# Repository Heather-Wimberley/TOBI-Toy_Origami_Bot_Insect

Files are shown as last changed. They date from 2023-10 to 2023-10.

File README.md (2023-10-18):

# Toy Origami Bot Insect (TOBI)

This repo details all of the supplementary files for a final-year engineering project.

## Description

Origami is an art form that folds paper into various shapes. These can range from a simple
butterfly to very many complicated patterns such as an intricate dragon. This idea has inspired
an engineering manufacturing technique, where the frame of a robot or other mechanical parts
are made to be assembled from a two-dimensional sheet to a three-dimensional pattern. This
allows for a more cost-effective manufacturing process and allows for easier storage and assembly
of the design. Translating the idea of folding paper to more robust objects can prove difficult
due to the complicated nature of the designs and the specialist equipment often required to
build these origami materials so this process is what the project aims to solve. This will be
done by designing a frame for a legged robot that will be used to entertain a cat. The robot
will need to be able to autonomously navigate a house while avoiding any obstacles in it.

A picture of the final robot made from the closed hardboard frame is found below.

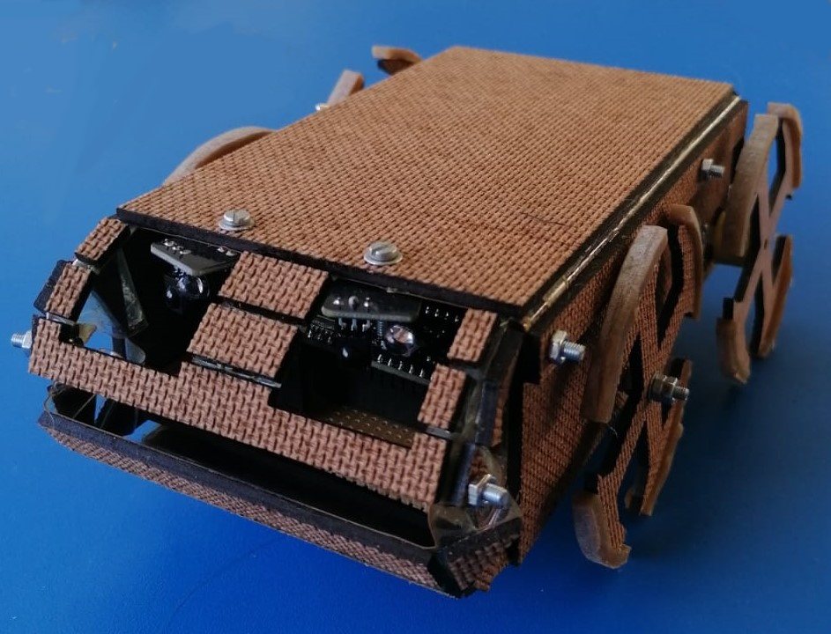
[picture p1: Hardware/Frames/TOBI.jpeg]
TOBI


## Contents
### Software

This file contains all the code written for the robot including design algorithms. The following files can be found:

- [OrigamiRobotAvoidance](Software/OrigamiRobotAvoidance.cpp):  The main function created for the robot to allow to avoid objects.
- [CurvedFrameSolver](Software/CurvedFrameSolver.mlx):  The algorithm is designed to be used with the curved frame to get the dimensions to be used for the curve. The height of the body and of the system and the number of segments can be changed to get the correct measurements. These are all assumed to be in mm.
- [Pickup](Software/Pickup.cpp):  This function contains the code for pickup detection working in isolation with the MXC6655. Due to time constraints, it was not integrated with the object avoidance.

### Hardware

This file contains the budget to see all components as well as all the .stl files of the whegs and each frame. This can be exported to pdfs to cut them using a laser cutter. A detailed breakdown of the files is:

- [Budget](Hardware/Budget.xlsx): This file is a spreadsheet of all the components, their prices and where they were acquired from. It also has the power budget done to determine battery requirements.
- [Electronics](Hardware/Electronics):  This folder contains the images needed to build the electronics of the robot. It includes a circuit diagram of the system as well as the veroboard design. The veroboard design includes the pin numbers that were used for the microcontroller.
- [Frames](Hardware/Frames):  This folder contains the stl files of all the frames designed. Although these are 3D, they are meant to be exported to a 2D pattern (top view) to be cut and the depth to the material has been added to show the different material parts. There are 5 designs of which two are made of posterboard and PET (labelled card) and three hardboard and vinyl (labelled wood). These materials each have different frame styles and assembly methods have been recorded in the associated paper.
- [Whegs](Hardware/Whegs):  This folder contains the stl files for the wheg design including the wheel caps for the back whegs and the two different versions that were designed.

## Authors

[Heather Wimberley](https://github.com/Heather-Wimberley)

## License

Open Source Project as long as creators are linked.

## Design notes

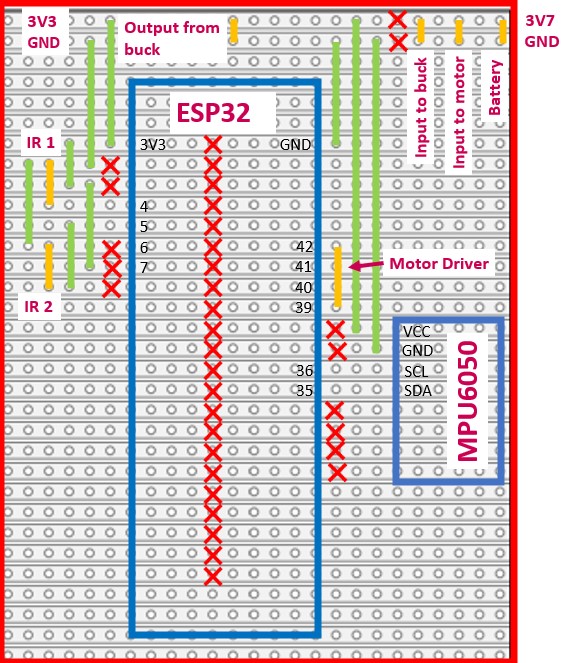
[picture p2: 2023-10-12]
Hardware/Electronics/Veroboard.jpg

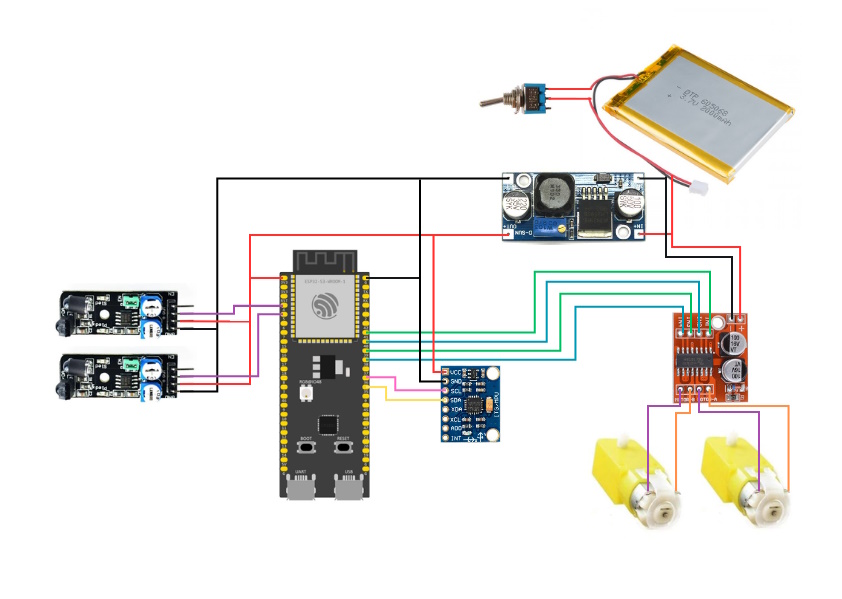
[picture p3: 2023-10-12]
Hardware/Electronics/Circuit Diagram.jpg

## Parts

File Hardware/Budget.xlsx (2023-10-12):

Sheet: Final Budget
Project Budget
Component | Price per unit | Quantity | Bought (B)/Owned (O) | Price | Total
HKD IR SENSOR SWITCH MODULE | 35.01 | 4 | B | 140.04 | 1049.64
BMT 3 AXIS ACCELEROMETER MPU6050 | 49 | 1 | B | 49
MX1616 H-BRG DC MOTOR DRIVER | 30 | 1 | B | 30
GEARED MOTOR 48:1 3-6VDC | 27 | 2 | B | 54
ESP32-S3-DevkitC-1 | 260 | 1 | O | 260
Battery LiPo 2000mAh 3.7V | 112 | 2 | B | 224
DC-DC STEP-DOWN | 52 | 1 | B | 52
Laminating sheets A4 | 1.4 | 9 |  | 12.6
Hardboard A3 | 18 | 4 |  | 72
Gluestick | 28 | 1 |  | 28
Posterboard (500gsm) | 16 | 8 |  | 128

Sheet: Electronics Comparison
Microcontrollers | Price | Link | Sensors | Price | Link | Battery | Price | Link
Raspberry Pi Zero W | 320 |  | BMT IR OBSTACLE AVOIDANCE SENSOR | 15 | https://www.communica.co.za/products/bmt-ir-obstacle-avoidance-sensor?variant=31803174682697 | HKD DC/DC BOOST MOD+USB 2-24V 2A | 29 | https://www.communica.co.za/products/hkd-dc-dc-boost-mod-usb-2-24v-2a?variant=45065768534316
ESP32-S3-DevkitC-1 | 260 | https://www.digikey.co.za/en/products/detail/espressif-systems/esp32-s3-devkitc-1-n32r8v/15970965 | HKD IR SENSOR SWITCH MODULE | 35.01 | https://www.communica.co.za/products/hkd-ir-sensor-switch-module?variant=31933933682761 |  | 26 | https://www.robofactory.co.za/power-converters/489-mt3608-dc-dc-2a-boost-module-2v-24v-with-micro-usb.html
 |  |  | BMT 3 AXIS ACCELEROMETER MPU6050 | 49 | https://www.communica.co.za/products/bmt-3-axis-accelerometer-mpu6050?variant=31667845464137 | 2XAA BATTERY HOLDER WITH SWITCH | 12 | https://www.communica.co.za/products/2xaa-battery-holder-with-switch?variant=17184817086537
 |  |  |  |  |  | AA Alkaline batteries x4 | 50 | https://www.takealot.com/energizer-e91bp3-1-1-5v-max-alkaline-aa-card-3-1-free/PLID69307304
 |  |  | MX1616 H-BRG DC MOTOR DRIVER | 30 | https://www.communica.co.za/products/bdd-mx1616-h-brg-dc-motor-driver?variant=45185422983468 | AA Lithium batteries x2 | 120 | https://www.takealot.com/energizer-ultimate-lithium-aa-2-pack/PLID15125839
 |  |  | DUAL MOTOR DRIVER L298 SCREW | 45 | https://www.communica.co.za/products/hkd-dual-motor-driver-l298-screw?variant=39943510523977
 |  |  | HKD DC MICRO MOTOR 3-6VDC 25MM | 11.5 | https://www.communica.co.za/products/hkd-dc-micro-motor-3-6vdc-25mm?variant=31932616638537 | 7.4V 1500MAH LI-ION BATTERY FOR HTRC5109 RC LEADING | 340 | https://denkit.co.za/product/7-4v-1500mah-li-ion-battery-for-htrc5109-rc-leading/
 |  |  | GEARED MOTOR 48:1 3-6VDC | 27 | https://www.communica.co.za/products/hkd-geared-motor-48-1-3-6vdc?variant=31933934043209 | NIMH 1500MAH 7.2 V BATTERY | 290 | https://denkit.co.za/product/nimh-1500mah-7-2-v-battery/
 |  |  |  |  |  | GT POWER N802 2A NIMH AC BATTERY CHARGER | 500 | https://gpmodels.co.za/products/n802-4-8s-nimh-nicd-charger
 |  |  |  |  |  | Battery LiPo 2000mAh 3.7V | 112 | https://www.robotics.org.za/DTP605068?search=battery
 |  |  |  |  |  | DC-DC STEP-DOWN | 52 | https://www.mantech.co.za/ProductInfo.aspx?Item=15M8180-A

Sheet: Power budget
Power Budget
Component | Typ. Voltage | Min Current (mA) | Typ. Current (mA) | Max Current (mA) | Min Power (W) | Typical Power (W) | Max Power (W)
ESP-32-S3-devkitc-1 | 3.3 | 500 |  |  | 1.65 |  |  | 1650
IR Sensors | 3.3 |  | 20 |  |  | 0.264 |  | 66
Accelerometer | 3.3 |  |  | 3.9 |  |  | 0.01287 | 12.87
Motor Driver | 3.7 |  |  | 30 |  |  | 0.111 | 111
Motors | 3.7 |  |  | 220 |  |  | 1.628 | 814
Total Power | 3.66587 | W |  | 7.33174 | Wh
Hours | 2 | hours |  | 1981.551351 | mAh
Voltage | 3.7 | V

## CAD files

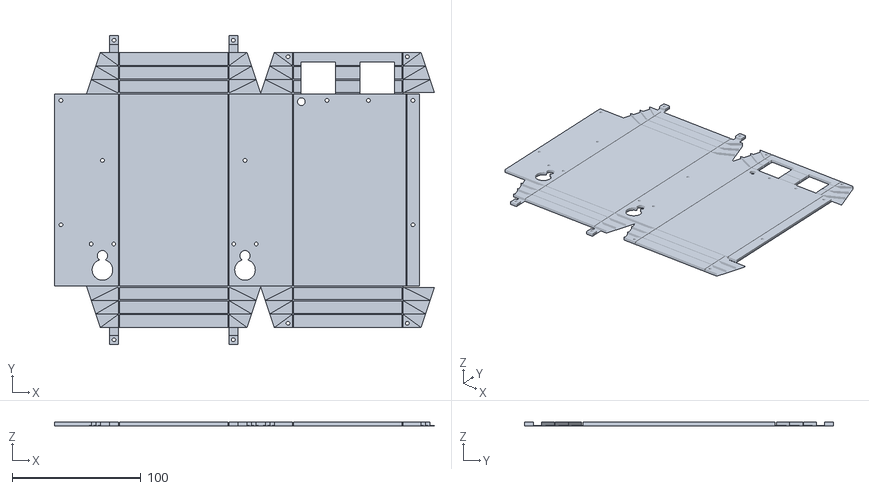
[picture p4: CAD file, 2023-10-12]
Hardware/Frames/ClosedFrameWood.stl
294.8 x 239.8 x 3.00

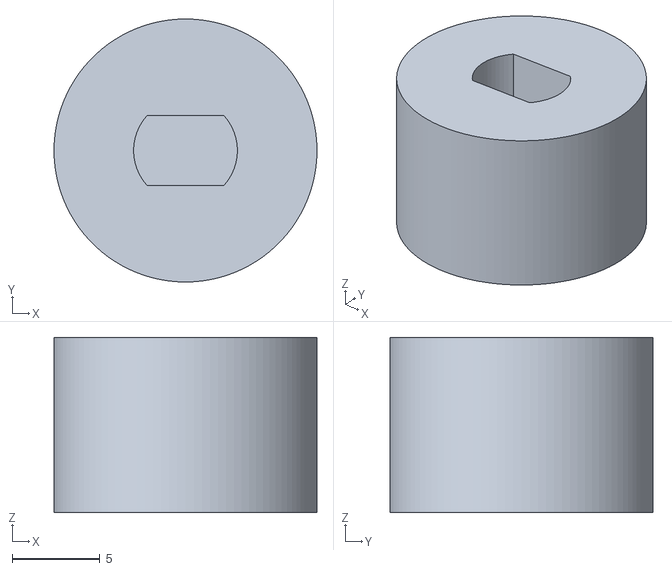
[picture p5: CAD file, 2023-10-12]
Hardware/Whegs/Wheel Hub.stl
15.0 x 15.0 x 10.0

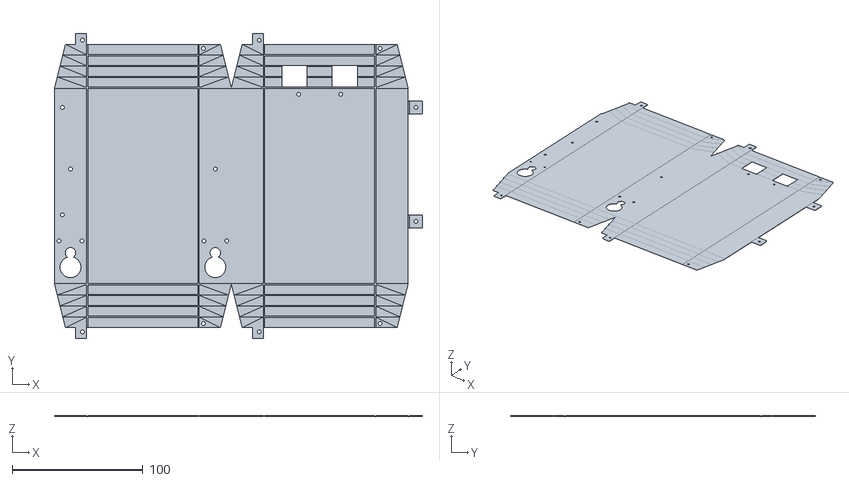
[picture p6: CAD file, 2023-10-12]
Hardware/Frames/ClosedFrameCard.stl
281.0 x 233.0 x 1.00

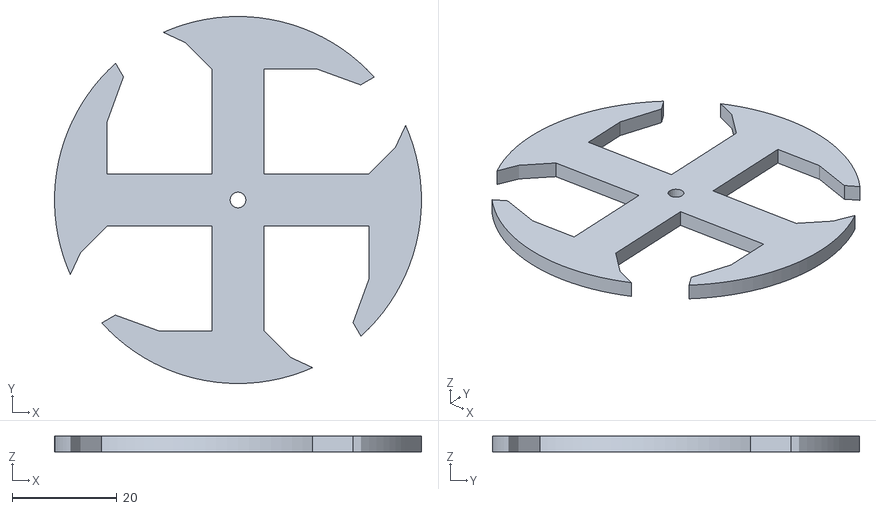
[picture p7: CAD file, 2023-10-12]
Hardware/Whegs/WhegsV2.stl
70.0 x 70.0 x 3.00

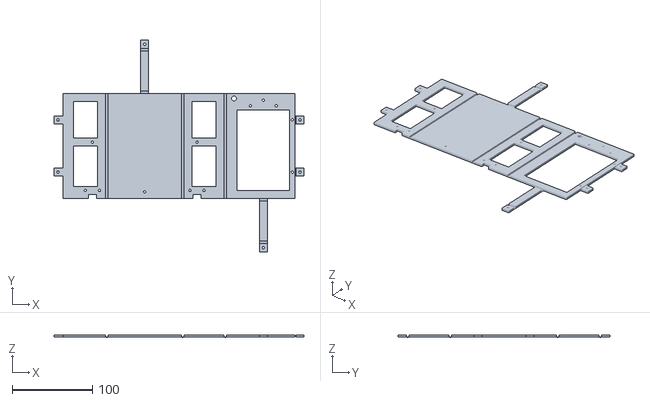
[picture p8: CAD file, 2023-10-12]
Hardware/Frames/OpenFrameWood-interlocking.stl
310.6 x 262.8 x 3.00

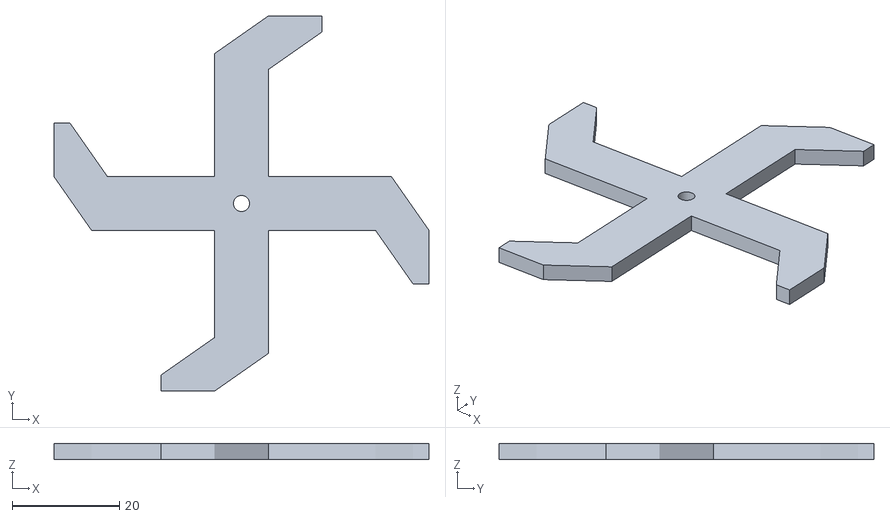
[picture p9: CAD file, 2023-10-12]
Hardware/Whegs/WhegV1.stl
70.0 x 70.0 x 3.00

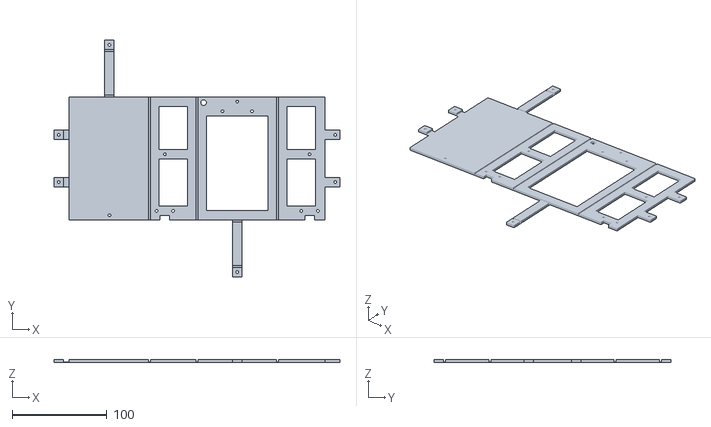
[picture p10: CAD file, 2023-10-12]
Hardware/Frames/OpenFrameWood.stl
302.2 x 250.0 x 3.00

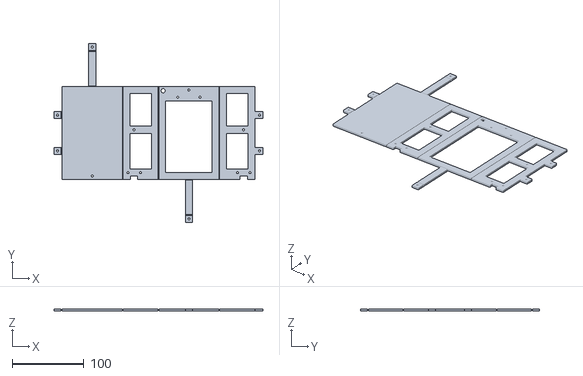
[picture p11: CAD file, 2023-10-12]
Hardware/Frames/OpenFrameCard.stl
292.0 x 250.0 x 3.00

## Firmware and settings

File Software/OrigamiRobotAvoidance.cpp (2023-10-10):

#include <Arduino.h>

// initialise pins
const int IR1 = 4; //Right IR sensor
const int IR2 = 5; //Left IR sensor
const int motorAp = 42; //IN1; Motor A is on right
const int motorAm = 41; //IN2; Motor A is on right
const int motorBp = 40; //IN3; Motor B is on left
const int motorBm = 39; //IN4; Motor B is on left

//current speed and angular velocity
int v = 0; //1 is forwards; 0 is stopped; -1 is backwards
int w = 0; //1 is clockwise; 0 is stopped; -1 is anticlockwise

int spinFlag = 0;

//create global IR array
int object [2];

//declare all functions
void getIR(void);
void calculateSpeed(void);
void setSpeed(void);

void setup() {
    // set IR pins as input
    pinMode(IR1,INPUT);
    pinMode(IR2,INPUT);

    // set all motor pins as output
    pinMode(motorAp,OUTPUT);
    pinMode(motorAm,OUTPUT);
    pinMode(motorBp,OUTPUT);
    pinMode(motorBm,OUTPUT);
}

void loop() {
    getIR();
    calculateSpeed();
    setSpeed();
}

void getIR(){

    int sensorVal [2] = {0,0};
    // freq = 200 Hz
    for (int i = 0;i<20;i++){
        sensorVal[0] += (1-digitalRead(IR1));
        sensorVal[1] += (1-digitalRead(IR2));
        delay(5);
    }

    if (sensorVal[0]>2){
        object[0] = 1;}
    else {
        object[0] = 0;}
    
    if (sensorVal[1]>2) {
        object[1] = 1; }
    else {
        object[1] = 0; }
}

void calculateSpeed(){
    if (spinFlag == 0){
        if (object[0]==0 && object[1] == 0) {
            spinFlag = 0;
        }
        else {
            spinFlag = 1;
        }
    }
    else {
        if (spinFlag<24){
            spinFlag +=1;
        }
        else{
            spinFlag = 100;
        }
    }
    
}

void setSpeed() {
    if (spinFlag == 0)
    {
        digitalWrite(motorAp,HIGH);
        digitalWrite(motorAm,LOW);
        digitalWrite(motorBp,HIGH);
        digitalWrite(motorBm,LOW);
    }

    if (spinFlag > 0 && spinFlag < 10)
    {
        digitalWrite(motorAp,LOW);
        digitalWrite(motorAm,HIGH);
        digitalWrite(motorBp,LOW);
        digitalWrite(motorBm,HIGH);
        if (spinFlag == 100) {
            spinFlag = 0;
        }
    }

    if (spinFlag >= 10)
    {
        digitalWrite(motorAp,LOW);
        digitalWrite(motorAm,HIGH);
        digitalWrite(motorBp,HIGH);
        digitalWrite(motorBm,LOW);
        if (spinFlag == 100) {
            spinFlag = 0;
        }
    }
}

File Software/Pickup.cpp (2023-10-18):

#include <Arduino.h>
#include <Wire.h>
#include "Accel_tilt.h"

#define INT 5
#define SLAVE_ADR 0x15
#define shakeInt 0x00
#define dataInt 0x01 //bit 7 - Tilt, bit 6 - z orientation+-, bit 5 - xy orientation bit 1 --> bit 4 xy orientation bit 0, bit 0, data ready
#define orient 0x02 
#define Xout 0x03 //goes to 0x04 upper at 0x03
#define Yout 0x05 // 2 bytes, upper at 0x05
#define Zout 0x07 // 2 bytes, upper at 0x07
#define Tout 0x09 //1 byte only
#define shakeIntSet 0x0A
#define dataAvailSet 0x0B
#define SDA 35
#define SCL 36

void getData(void);

#define FSR8 0b01000000 //8g operation
#define FSR2 0b00000000 //2g operation
#define FSR8_SCALE 256.0 //8g operation scaling factor
#define FSR2_SCALE 1024.0 //2g operation scaling factor

//storage for accelerometer
double ZVal = 0;
double avgZ = 0;
double prevZ = 0;
double Zoffset = 0;
int moveCount = 0;
int pickup = 0;

void setup()
{
    // Start I2C transmission and serial comms
    delay(400);

    Wire.begin(SDA,SCL);
    Serial.begin(115200);

    // Initialise the accelerometer interrupts to 0
    Wire.beginTransmission(SLAVE_ADR);
    Wire.write(shakeInt);
    Wire.write(0);
    Wire.endTransmission();

    // Initialise the accelerometer data collects to 0
    Wire.beginTransmission(SLAVE_ADR);
    Wire.write(dataInt);
    Wire.write(0);
    Wire.endTransmission();

    //configure range of FSRs
    Wire.beginTransmission(SLAVE_ADR); 
    Wire.write(0x0D);
    Wire.write(FSR8);
    Wire.endTransmission();

    // disable temperature compensation 0x80 else 0x00
    Wire.beginTransmission(SLAVE_ADR); 
    Wire.write(0x0B);
    Wire.write(0x00);
    Wire.endTransmission();

    //configure shake interrupts -- not used
    Wire.beginTransmission(SLAVE_ADR);
    Wire.write(0x0C);
    Wire.write(0b10001000);
    Wire.endTransmission();

    //calculate the starting orientation of the accelerometer
    for (int counter = 0;counter<100;counter++){
        getData();
        delay(1);
        avgZ += ZVal*0.01; //equal avegrage of 100 values
    }

    //add offset based on assumption that +z axis is up and avgZ should be 1g due to gravity
    Zoffset = 1-(avgZ/FSR8_SCALE);
}

void loop()
{
    
    // fetch data from accelerometer via I2C
    for (int i = 0; i<20;i++){
        prevZ = ZVal;
        getData();
        if(abs(prevZ-ZVal)>=1)
        {
            moveCount += 1;
        }
        delay(5);
    }

    if (moveCount>2)
    {
        Serial.println("Pickup detected");
        moveCount = 0;
    }
}

void getData(){ // Retreives data from the accelerometer via I2C
  Wire.beginTransmission(SLAVE_ADR);
  Wire.write(0);
  Wire.endTransmission();

  Wire.requestFrom(SLAVE_ADR, 10);
  Wire.read();
  int dataByte = Wire.read();

  
  if (bitRead(dataByte, 0)){ // Check whether new data is available from the accelerometer
    int orientByte = Wire.read();

    int Byte1 = Wire.read();
    int Byte2 = Wire.read();
    int XVal = ((Byte1<<24)|(Byte2<<16))>>20;

    Byte1 = Wire.read();
    Byte2 = Wire.read();
    int YVal = ((Byte1<<24)|(Byte2<<16))>>20;

    Byte1 = Wire.read();
    Byte2 = Wire.read();
    ZVal = ((Byte1<<24)|(Byte2<<16))>>20;

    ZVal = ZVal/FSR8_SCALE + Zoffset;

    Byte1 = Wire.read();
    int temp = (Byte1<<24)>>24;
    int tempf = 25 + temp*0.586;
  }
  else{ // else just read data into nothing to clear transmission out
    Wire.read();
    Wire.read();
    Wire.read();
    Wire.read();
    Wire.read();
    Wire.read();
    Wire.read();
    Wire.read();
  }
  
}

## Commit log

2023-10-10 Add object avoidance code
    [OrigamiRobotAvoidance.cpp]
2023-10-12 Add all design files
    [Budget.xlsx, ClosedFrameCard.stl, ClosedFrameWood.stl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]
